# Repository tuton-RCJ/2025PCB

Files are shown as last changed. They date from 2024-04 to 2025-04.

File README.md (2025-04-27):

# 2025PCB
ツートンの基板・回路のリポジトリです。
ご自由にご覧下さい。

基板はすべてKiCAD7.0で設計し、JLCPCB様に発注しています。
1-TOKYOが東東京ノード大会で使用した基板です。
2-KANTOは関東ブロック大会で使用した基板です。
3-NAGOYAは名古屋全国大会で使用した基板です。

# 3-NAGOYA
全国大会機「シロ」の基板です。
全部で6枚です。
## 基板一覧
* 01 MAIN
    メイン基板。一層目に置きます。
* 02 LINE
    ラインセンサ基板。一層目に置きます。
    フォトリフレクタは16個使います。
* 03 FRONT
    正面基板。ToFセンサを搭載しています。
* 04 RESCUE
    二層目と一層目をつなぐ基板です。
* 05 PWR
    電源基板。メイン基板とスペーサで接続します。
* 06 UI
    UI基板。ディスプレイを搭載しています。使いませんでした。
* 07 OpenMV
    OpenMVに取り付けるシールドです。UARTをXHに引き出しました。

# 2-KANTO
関東機体「MIKE（ミケ）」の基板です。
今回は全部で3枚です。

## 基板一覧
* 01 MAIN
    メイン基板。一層目に置きます。
* 02 LINE
    ラインセンサ基板。一層目に置きます。
    フォトリフレクタは16個使います。
* 03 FRONT
    当初は作る予定だったが使わなくなりました。
    空っぽなのもつまらないので回路図に落書きしました。
* 04 PWR
    電源基板。二層目に置きます。

# 1-TOKYO
東東京機体「ポチ」の基板です。
全部で5枚（+α）です。

## 基板一覧
* 01 main
    メイン基板。
    * 完成 2024/10/01
    * 発注 2024/10/02
* 02 top
    ハンドルの上に置く基板。UI基板。
    * 設計中
    * 使わなかった
* 03 front
    正面の基板。カメラとToFを置く。
    * 完成 2024/10/01
    * 発注 2024/10/02
* 04 line
    ラインセンサ基板。
    * 完成 2024/06/25
    * 発注 2024/06/26
* 05 PWR
    電源基板。
    3.3V, 5V, 7.2Vを生成。
    * 完成 2024/06/25
    * 発注 2024/06/26
* 06 WRITER
    書き込み基板
    * 完成 2024/05/14
    * 発注 2024/05/16
* 07 frame
    フレームを基板で作ろうとしたが結局3Dプリンタで作った。
* 08 REG_mod
    TPS5430を使用した自作DCDC。
    電源基板に乗せる。
    * 完成 2024/06/25
    * 発注 2024/06/26
* 09 ToF_mod
    自作ToF（VL53L0X）
    * 完成　2024/08/17
## リポジトリ構成
* 01-main ~ 08-REG_mod 
    それぞれの基板のKiCADのプロジェクト。
* library
    KiCADで使用しているライブラリ。
    シンボル、フットプリント、3Dモデル。
* pin
    STM32のピン配置を考えるために使用したSTM32CubeIDEのファイル。
    かなり雑です。
* ver1、ver2
    過去作の保管場所。
    何らかの事情でボツになった設計たちです。
* PDFファイル
    完成した基板の回路図はPDFにしてあります。
    ブラウザ上で見ることができると思います。

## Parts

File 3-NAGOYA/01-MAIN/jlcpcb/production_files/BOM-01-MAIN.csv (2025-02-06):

Comment | Designator | Footprint | LCSC
FerriteBead | FB1 | R_0805_2012Metric | C1015
100n | C1,C10,C12,C13,C3,C4,C5,C6,C8,C9 | C_0402_1005Metric | C1525
10u | C14,C15 | C_0805_2012Metric | C15850
1k | R8 | R_0805_2012Metric | C17513
USB_C_Receptacle_USB2.0 | J4 | USB_C_Receptacle_GCT_USB4105-xx-A_16P_TopMnt_Horizontal | C19274016
LED_ORANGE | D4 | LED_0805_2012Metric | C2296
LED_GREEN | D1,D2,D3,D7,D8 | LED_0805_2012Metric | C2297
470 | R10,R12,R17,R18,R7 | R_0603_1608Metric | C23179
7.5k | R1 | R_0603_1608Metric | C23234
4.7u | C2,C7 | C_0402_1005Metric | C23733
10k | R13,R15,R2,R6 | R_0603_1608Metric | C25804
5.1k | R11,R9 | R_0805_2012Metric | C27834
20k | R3 | R_0603_1608Metric | C4184
2.2k | R14,R16,R4,R5 | R_0603_1608Metric | C4190
22u | L1,L2 | FXL1040-220-M | C475917
1u | C11 | C_0402_1005Metric | C52923
0.01u | C16,C17 | C_0603_1608Metric | C57112
MAX485ESA | U2 | SOP-8_3.9x4.9mm_P1.27mm | C668206
STM32F446RETx | U1 | LQFP-64_10x10mm_P0.5mm | C69336
SS34 | D5,D6 | D_SMA | C8678
TPS5430DDA | U7,U8 | TI_SO-PowerPAD-8_ThermalVias | C9864
CH340E | U6 | MSOP-10_3x3mm_P0.5mm | C99652
~ | U4 | BNO055
Front | J1 | JST_XH_B4B-XH-A_1x04_P2.50mm_Vertical
toLINE | J3 | JST_XH_B5B-XH-A_1x05_P2.50mm_Vertical
STS3032 | J5 | Molex_SPOX_5267-03A_1x03_P2.50mm_Vertical
2SA1015 | Q1 | TO-92_Inline
STS3032 | J8 | Molex_SPOX_5267-03A_1x03_P2.50mm_Vertical
STS3032 | J7 | Molex_SPOX_5267-03A_1x03_P2.50mm_Vertical
220u | C18 | CP_Radial_D6.3mm_P2.50mm
~ | U5 | vl53l0x_vertical
STS3032 | J6 | Molex_SPOX_5267-03A_1x03_P2.50mm_Vertical
~ | U3 | vl53l0x_vertical
Top | J2 | JST_XH_B4B-XH-A_1x04_P2.50mm_Vertical
220u | C19 | CP_Radial_D6.3mm_P2.50mm
Buzzer | BZ1 | Buzzer_15x7.5RM7.6
NRST | SW1 | THBP07-043Cx
BOOT0 | SW2 | THBP07-043Cx

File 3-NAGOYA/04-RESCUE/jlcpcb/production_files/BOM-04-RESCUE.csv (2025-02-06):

Comment | Designator | Footprint | LCSC
100n | C10,C11,C12,C14,C15,C8,C9 | C_0402_1005Metric | C1525
10k | R12,R13 | R_1206_3216Metric | C17902
1M | R10,R7,R8,R9 | R_0603_1608Metric | C22935
LED_GREEN | D1 | LED_0805_2012Metric | C2297
330 | R1,R2,R3,R6 | R_0603_1608Metric | C23138
470 | R11 | R_0603_1608Metric | C23179
4.7u | C13 | C_0402_1005Metric | C23733
10k | R4,R5 | R_0603_1608Metric | C25804
22u | C1,C2 | C_0805_2012Metric | C45783
LM358 | U1 | SOIC-8_3.9x4.9mm_P1.27mm | C5423
AMS1117-3.3 | U5 | SOT-223-3_TabPin2 | C6186
STM32F103RCTx | U4 | LQFP-64_10x10mm_P0.5mm | C8323
ServoArmRight | M4 | PinHeader_1x03_P2.54mm_Horizontal
MAIN | J2 | JST_XH_B4B-XH-A_1x04_P2.50mm_Vertical
OpenMV | J6 | JST_XH_B4B-XH-A_1x04_P2.50mm_Vertical
ServoHandLeft | M5 | PinHeader_1x03_P2.54mm_Horizontal
ServoArmLeft | M3 | PinHeader_1x03_P2.54mm_Horizontal
UI | J1 | JST_XH_S4B-XH-A_1x04_P2.50mm_Horizontal
ServoHandRight | M6 | PinHeader_1x03_P2.54mm_Horizontal
LOADCELL_L | J5 | JST_XH_S4B-XH-A_1x04_P2.50mm_Horizontal
~ | U2 | vl53l0x_vertical
LOADCELL_R | J3 | JST_XH_S4B-XH-A_1x04_P2.50mm_Horizontal
ServoBasketLeft | M1 | PinHeader_1x03_P2.54mm_Horizontal
~ | U3 | vl53l0x_vertical
WRITER CONN | J4 | PinSocket_2x04_P2.54mm_Vertical

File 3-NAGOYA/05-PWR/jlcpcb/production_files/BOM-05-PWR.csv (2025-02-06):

Comment | Designator | Footprint | LCSC
10uF | C3,C4 | C_0805_2012Metric | C15850
1k | R1 | R_0603_1608Metric | C21190
1.2k | R6,R7 | R_0603_1608Metric | C22765
1.5k | R4 | R_0603_1608Metric | C22843
10 | R3 | R_0603_1608Metric | C22859
330 | R2 | R_0603_1608Metric | C23138
680 | R5 | R_0603_1608Metric | C23228
10k | R8 | R_0603_1608Metric | C25804
22uF | C1,C2 | C_0805_2012Metric | C45783
Fuse | F1 | FUSE_3557-15
~ | U2 | OKL-T6-W12N-C-SMD
Q_PMOS_GDS | Q1 | TO-251-3_Vertical
SW_SPST | SW1 | AkizukiSmallRockerSwitchHorizontal
~ | U1 | OKL-T6-W12N-C-SMD

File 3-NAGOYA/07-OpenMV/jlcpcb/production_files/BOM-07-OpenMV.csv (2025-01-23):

Comment | Designator | Footprint | LCSC
Conn_01x04 | J3 | JST_XH_S4B-XH-A_1x04_P2.50mm_Horizontal
3V3IN | SW2 | SK-12D11VG3
5VIN | SW1 | SK-12D11VG3
REG | J4 | PinHeader_1x03_P2.54mm_Vertical
OpenMV2 | J2 | PinSocket_1x08_P2.54mm_Vertical
OpenMV1 | J1 | PinSocket_1x08_P2.54mm_Vertical
LED | D2 | LED_D3.0mm_Clear
5VLED | D1 | LED_D3.0mm_Clear

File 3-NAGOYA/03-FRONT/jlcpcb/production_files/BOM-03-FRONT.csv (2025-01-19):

Comment | Designator | Footprint | LCSC
MountingHole | H2 | MountingHole_3.2mm_M3
WS2812B | D1 | LED_WS2812B_PLCC4_5.0x5.0mm_P3.2mm
~ | U5 | VL53L0X_horizontal
WS2812B | D4 | LED_WS2812B_PLCC4_5.0x5.0mm_P3.2mm
WS2812B | D2 | LED_WS2812B_PLCC4_5.0x5.0mm_P3.2mm
~ | U2 | VL53L0X_horizontal
WS2812B | D5 | LED_WS2812B_PLCC4_5.0x5.0mm_P3.2mm
MountingHole | H1 | MountingHole_3.2mm_M3
~ | U4 | VL53L0X_horizontal
WS2812B | D3 | LED_WS2812B_PLCC4_5.0x5.0mm_P3.2mm
~ | U3 | VL53L0X_horizontal
~ | U1 | VL53L0X_horizontal
10k | R1 | R_Axial_DIN0207_L6.3mm_D2.5mm_P10.16mm_Horizontal
OpenMV Conn | J1 | JST_XH_B4B-XH-A_1x04_P2.50mm_Vertical
10k | R2 | R_Axial_DIN0207_L6.3mm_D2.5mm_P10.16mm_Horizontal
~ | U6 | MOUDLE14P-2.54-21X17.8MM

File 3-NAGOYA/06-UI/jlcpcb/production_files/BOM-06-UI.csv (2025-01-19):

Comment | Designator | Footprint | LCSC
OpenMV Conn | J1 | JST_XH_S4B-XH-A_1x04_P2.50mm_Horizontal
~ | U1 | MOUDLE14P-SMD-2.54-21X17.8MM
~ | U2 | MS2807
SW_Push | SW1 | SW_PUSH-12mm
R | R1 | R_Axial_DIN0207_L6.3mm_D2.5mm_P10.16mm_Horizontal
MountingHole | H2 | MountingHole_3.2mm_M3
MountingHole | H1 | MountingHole_3.2mm_M3
WS2812B | D8 | LED_WS2812B_PLCC4_5.0x5.0mm_P3.2mm
WS2812B | D7 | LED_WS2812B_PLCC4_5.0x5.0mm_P3.2mm
WS2812B | D6 | LED_WS2812B_PLCC4_5.0x5.0mm_P3.2mm
WS2812B | D5 | LED_WS2812B_PLCC4_5.0x5.0mm_P3.2mm
WS2812B | D4 | LED_WS2812B_PLCC4_5.0x5.0mm_P3.2mm
WS2812B | D3 | LED_WS2812B_PLCC4_5.0x5.0mm_P3.2mm
WS2812B | D2 | LED_WS2812B_PLCC4_5.0x5.0mm_P3.2mm
WS2812B | D1 | LED_WS2812B_PLCC4_5.0x5.0mm_P3.2mm

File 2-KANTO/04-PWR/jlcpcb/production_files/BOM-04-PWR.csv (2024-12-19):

Comment | Designator | Footprint | LCSC
100n | C1,C2,C3,C4,C5,C6 | C_0402_1005Metric | C1525
10uF | C10,C11 | C_0805_2012Metric | C15850
1k | R7 | R_0603_1608Metric | C21190
1.2k | R12,R13 | R_0603_1608Metric | C22765
1.5k | R10 | R_0603_1608Metric | C22843
10 | R9 | R_0603_1608Metric | C22859
LED_GREEN | D1 | LED_0805_2012Metric | C2297
330 | R8 | R_0603_1608Metric | C23138
470 | R5 | R_0603_1608Metric | C23179
680 | R11 | R_0603_1608Metric | C23228
4.7u | C7 | R_0402_1005Metric | C23733
10k | R1,R2,R3,R4,R6 | R_0603_1608Metric | C25804
22uF | C8,C9 | C_0805_2012Metric | C45783
STM32F103C8Tx | U1 | LQFP-48_7x7mm_P0.5mm | C8734
~ | U5 | OKL-T6-W12N-C-SMD
SW_SPST | SW2 | AkizukiSmallRockerSwitchHorizontal
~ | U4 | OKL-T6-W12N-C-SMD
MAIN Conn | J5 | JST_XH_S8B-XH-A_1x08_P2.50mm_Horizontal
ServoHandRight | M6 | PinHeader_1x03_P2.54mm_Horizontal
Fuse | F1 | FUSE_3557-15
~ | U2 | vl53l0x_vertical
WRITER CONN | J4 | PinSocket_2x04_P2.54mm_Horizontal
~ | U3 | vl53l0x_vertical
Conn_01x05 | J2 | PinHeader_1x05_P2.54mm_Vertical
ServoArmRight | M4 | PinHeader_1x03_P2.54mm_Horizontal
ServoHandLeft | M5 | PinHeader_1x03_P2.54mm_Horizontal
voltmeter | J7 | JST_XH_S2B-XH-A_1x02_P2.50mm_Horizontal
OpenMV Conn | J6 | JST_XH_S4B-XH-A_1x04_P2.50mm_Horizontal
Q_PMOS_GDS | Q1 | TO-251-3_Vertical
PA_PIN | J3 | PinHeader_1x16_P2.54mm_Vertical
ServoArmLeft | M3 | PinHeader_1x03_P2.54mm_Horizontal
PB_PIN | J1 | PinHeader_1x16_P2.54mm_Vertical
SW_SPDT | SW1 | SK-12D11VG3
ServoBasketLeft | M1 | PinHeader_1x03_P2.54mm_Vertical

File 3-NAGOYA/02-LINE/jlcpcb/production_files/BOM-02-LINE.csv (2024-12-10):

Comment | Designator | Footprint | LCSC
FerriteBead | FB1 | R_0805_2012Metric | C1015
100n | C1,C3,C4,C5,C6,C8,C9 | C_0402_1005Metric | C1525
1k | R16,R17,R18,R19,R20,R21,R22,R23,R32,R33,R34,R35,R36,R37,R38,R39 | R_0603_1608Metric | C21190
120 | R10,R11,R12,R13,R14,R15,R24,R25,R26,R27,R28,R29,R30,R31,R8,R9 | R_0603_1608Metric | C22787
LED_GREEN | D1 | LED_0805_2012Metric | C2297
470 | R3 | R_0603_1608Metric | C23179
4.7u | C2,C7 | C_0402_1005Metric | C23733
10k | R1,R2 | R_0603_1608Metric | C25804
1u | C10 | C_0402_1005Metric | C52923
STM32F446RETx | U1 | LQFP-64_10x10mm_P0.5mm | C69336
Conn_01x05 | J3 | JST_XH_B5B-XH-A_1x05_P2.50mm_Vertical
~ | U16 | LBR127HLD
WS2812B | D5 | LED_WS2812B_PLCC4_5.0x5.0mm_P3.2mm
WS2812B | D6 | LED_WS2812B_PLCC4_5.0x5.0mm_P3.2mm
WS2812B | D4 | LED_WS2812B_PLCC4_5.0x5.0mm_P3.2mm
~ | U17 | LBR127HLD
~ | U7 | LBR127HLD
~ | U6 | LBR127HLD
~ | U3 | LBR127HLD
~ | U9 | LBR127HLD
~ | U12 | LBR127HLD
~ | U8 | LBR127HLD
~ | U10 | LBR127HLD
~ | U5 | LBR127HLD
~ | U14 | LBR127HLD
WS2812B | D3 | LED_WS2812B_PLCC4_5.0x5.0mm_P3.2mm
~ | U2 | LBR127HLD
~ | U13 | LBR127HLD
WS2812B | D2 | LED_WS2812B_PLCC4_5.0x5.0mm_P3.2mm
WS2812B | D7 | LED_WS2812B_PLCC4_5.0x5.0mm_P3.2mm
~ | U11 | LBR127HLD
~ | U4 | LBR127HLD
WRITER CONN | J2 | PinSocket_2x04_P2.54mm_Vertical
~ | U15 | LBR127HLD
~ | U19 | S9706
~ | U18 | S9706

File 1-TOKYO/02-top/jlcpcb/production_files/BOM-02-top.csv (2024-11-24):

Comment | Designator | Footprint | LCSC
ToTop | J1 | JST_XH_B4B-XH-A_1x04_P2.50mm_Vertical
SW_Push | SW3 | SW_PUSH_6mm
SW_Push | SW2 | SW_PUSH_6mm
SW_Push | SW1 | SW_PUSH_6mm
WS2812B | D3 | LED_WS2812B_PLCC4_5.0x5.0mm_P3.2mm
WS2812B | D4 | LED_WS2812B_PLCC4_5.0x5.0mm_P3.2mm
WS2812B | D6 | LED_WS2812B_PLCC4_5.0x5.0mm_P3.2mm
SSD1306 | J2 | PinHeader_1x04_P2.54mm_Vertical
WS2812B | D2 | LED_WS2812B_PLCC4_5.0x5.0mm_P3.2mm
SW_SPDT | SW4 | PinHeader_1x03_P2.54mm_Vertical
WS2812B | D1 | LED_WS2812B_PLCC4_5.0x5.0mm_P3.2mm
WS2812B | D5 | LED_WS2812B_PLCC4_5.0x5.0mm_P3.2mm
~ | U1 | XIAO_Board
10k | R1 | R_Axial_DIN0207_L6.3mm_D2.5mm_P10.16mm_Horizontal
10k | R3 | R_Axial_DIN0207_L6.3mm_D2.5mm_P10.16mm_Horizontal
10k | R2 | R_Axial_DIN0207_L6.3mm_D2.5mm_P10.16mm_Horizontal
10k | R4 | R_Axial_DIN0207_L6.3mm_D2.5mm_P10.16mm_Horizontal

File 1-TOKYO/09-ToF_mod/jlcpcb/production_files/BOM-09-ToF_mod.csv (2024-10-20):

Comment | Designator | Footprint | LCSC
0.1u | C1 | C_0603_1608Metric | C14663
4.7u | C2 | C_0603_1608Metric | C19666
1.5k | R2,R3 | R_0603_1608Metric | C22843
10k | R1,R4 | R_0603_1608Metric | C25804
VL53L0X | U1 | ST_VL53L0X | C91199
Conn_01x02 | J2 | PinHeader_1x02_P2.54mm_Vertical
Conn_01x04 | J1 | PinHeader_1x04_P2.54mm_Vertical

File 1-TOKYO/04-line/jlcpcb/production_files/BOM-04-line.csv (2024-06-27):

Comment | Designator | Footprint | LCSC
100n | C3,C6 | C_0402_1005Metric | C1525
1k | R10,R11,R12,R13,R14,R15,R16,R17,R18,R28,R29,R30,R31,R32,R33,R34 | R_0603_1608Metric | C21190
120 | R1,R19,R2,R20,R21,R22,R23,R24,R25,R3,R4,R5,R6,R7,R8,R9 | R_0603_1608Metric | C22787
WS2812B | D1,D2,D4,D5,D6,D8 | LED_WS2812B_PLCC4_5.0x5.0mm_P3.2mm | C2843785
Conn_01x18 | J1 | PinHeader_1x18_P2.54mm_Vertical
CS_L | J3 | PinHeader_2x03_P2.54mm_Vertical
~ | U2 | LBR127HLD
~ | U15 | LBR127HLD
~ | U14 | LBR127HLD
~ | U25 | S11059
~ | U7 | LBR127HLD
~ | U4 | LBR127HLD
~ | U5 | LBR127HLD
~ | U16 | LBR127HLD
~ | U17 | LBR127HLD
~ | U8 | LBR127HLD
~ | U12 | LBR127HLD
~ | U3 | LBR127HLD
~ | U26 | S11059
~ | U9 | LBR127HLD
~ | U18 | LBR127HLD
~ | U6 | LBR127HLD
~ | U10 | LBR127HLD
~ | U13 | LBR127HLD
CS_R | J2 | PinHeader_2x03_P2.54mm_Vertical

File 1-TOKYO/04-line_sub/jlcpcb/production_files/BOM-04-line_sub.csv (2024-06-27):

Comment | Designator | Footprint | LCSC
FerriteBead | FB1 | R_0805_2012Metric | C1015
100n | C1,C3,C4,C5,C6,C8,C9 | C_0402_1005Metric | C1525
1u | C10 | C_0603_1608Metric | C15849
10k | R1,R2,R4,R5,R6,R7 | R_0805_2012Metric | C17414
LED_GREEN | D1 | LED_0805_2012Metric | C2297
470 | R3 | R_0603_1608Metric | C23179
4.7u | C2,C7 | C_0402_1005Metric | C23733
STM32F446RETx | U1 | LQFP-64_10x10mm_P0.5mm | C69336
Conn_01x18 | J4 | PinHeader_1x18_P2.54mm_Vertical
CS_R | J3 | PinHeader_2x03_P2.54mm_Vertical
Conn_01x06 | J1 | JST_XH_B6B-XH-A_1x06_P2.50mm_Vertical
WRITER CONN | J2 | PinHeader_2x04_P2.54mm_Vertical
CS_L | J5 | PinHeader_2x03_P2.54mm_Vertical

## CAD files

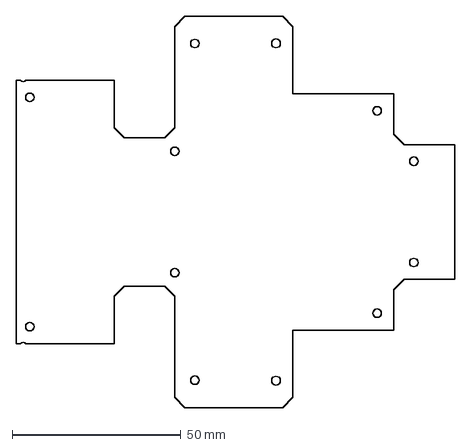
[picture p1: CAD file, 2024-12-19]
2-KANTO/01-MAIN/01-main-outline.dxf
130.0 x 116.0 mm

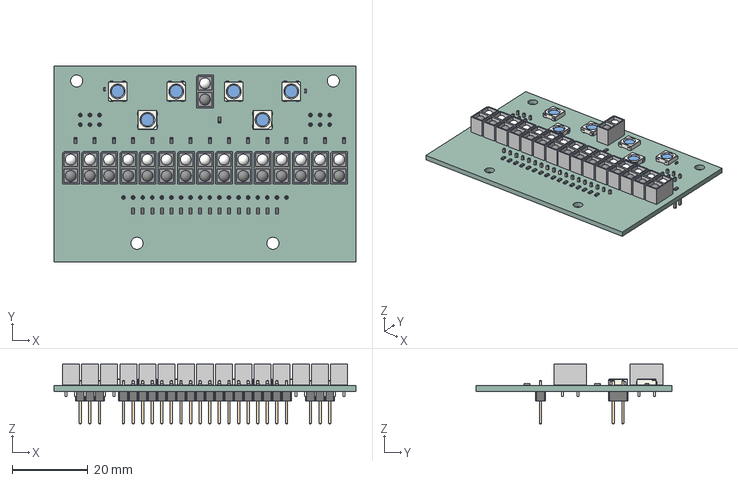
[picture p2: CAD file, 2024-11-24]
1-TOKYO/04-line/04-line.step
80.0 x 52.0 x 15.8 mm
04-line PCB

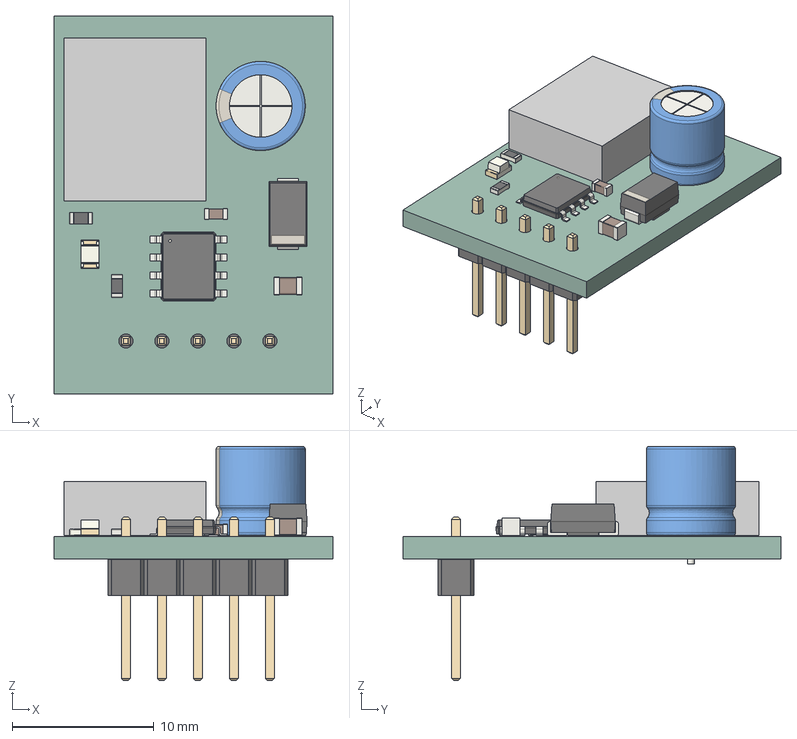
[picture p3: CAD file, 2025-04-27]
1-TOKYO/08-REG_mod/08-REG_mod_horizontal.step
19.7 x 26.7 x 16.5 mm
_autosave-08-REG_mod PCB

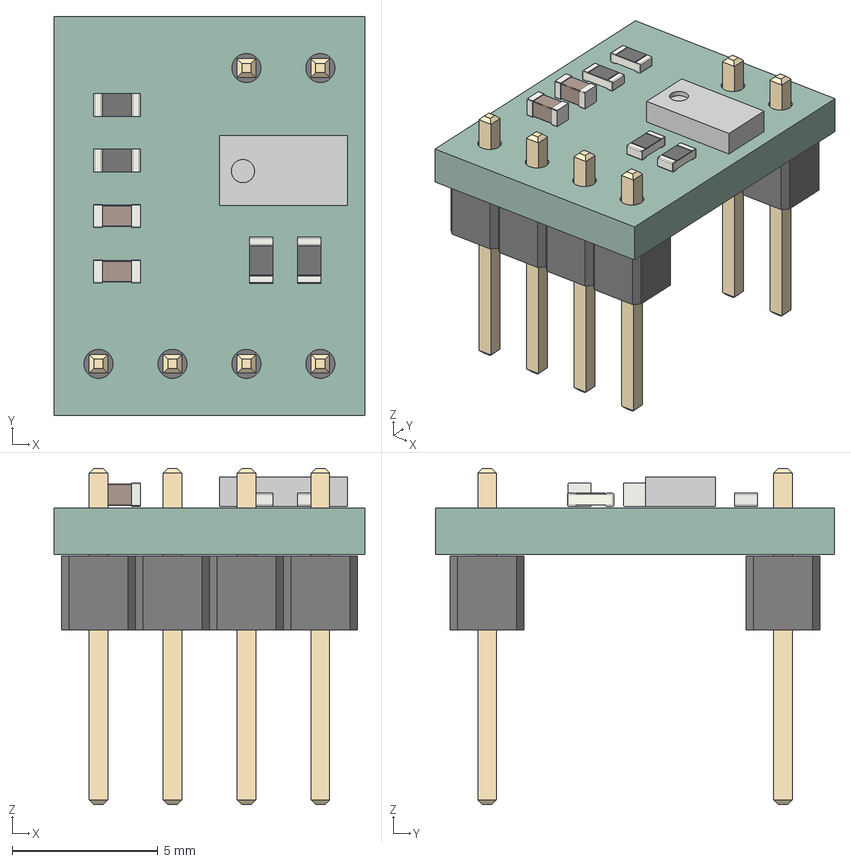
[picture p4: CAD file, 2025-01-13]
1-TOKYO/09-ToF_mod/09-ToF_mod_horizontal.step
10.7 x 13.7 x 11.5 mm
09-ToF_mod PCB

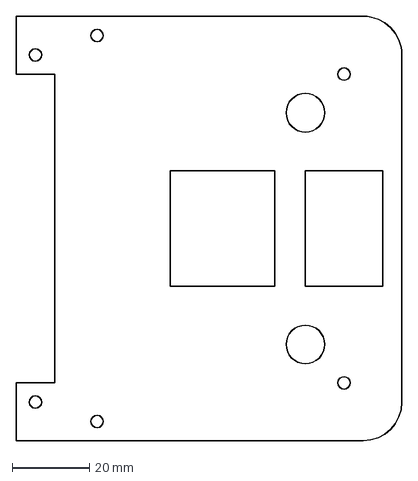
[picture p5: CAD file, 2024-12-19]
2-KANTO/04-PWR/POWER_OUTLINE.dxf
100.0 x 110.0 mm

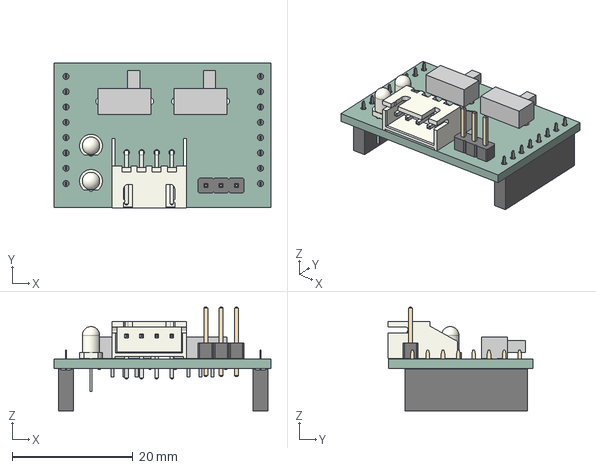
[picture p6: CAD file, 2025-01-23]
3-NAGOYA/07-OpenMV/07-OpenMV.step
36.0 x 24.0 x 17.2 mm
_autosave-07-OpenMV PCB

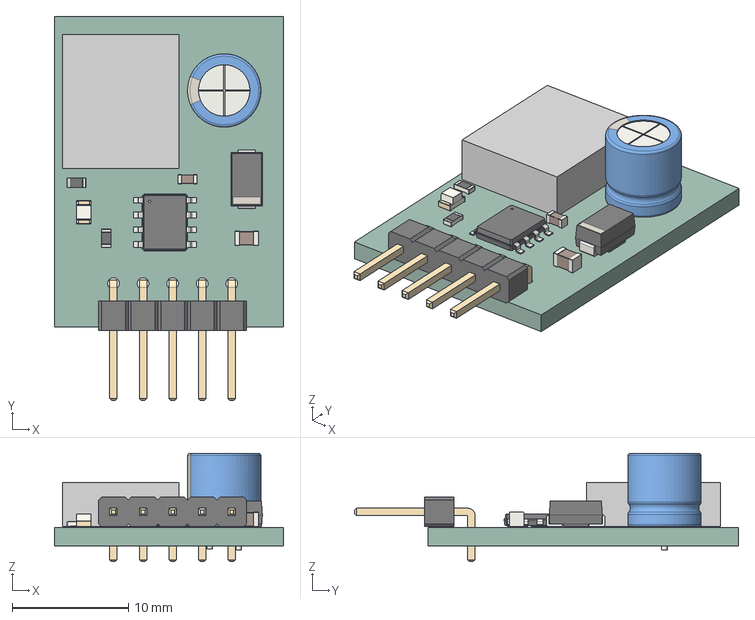
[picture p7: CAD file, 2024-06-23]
1-TOKYO/08-REG_mod/08-REG_mod.step
19.7 x 33.0 x 9.30 mm
08-REG_mod PCB

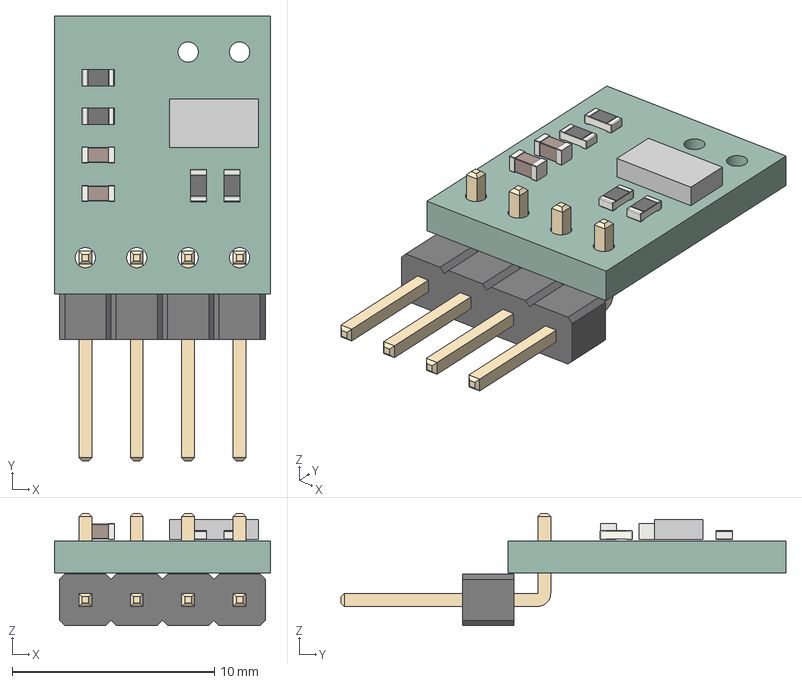
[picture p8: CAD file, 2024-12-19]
1-TOKYO/09-ToF_mod/09-ToF_mod_vertical.step
10.7 x 22.0 x 5.54 mm
09-ToF_mod PCB

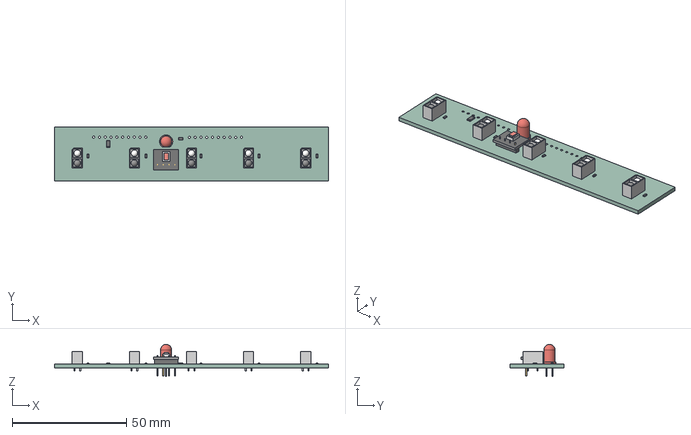
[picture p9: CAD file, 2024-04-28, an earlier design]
1-TOKYO/ver1/03-front/03-front.step
120.0 x 23.6 x 14.1 mm
03-front PCB

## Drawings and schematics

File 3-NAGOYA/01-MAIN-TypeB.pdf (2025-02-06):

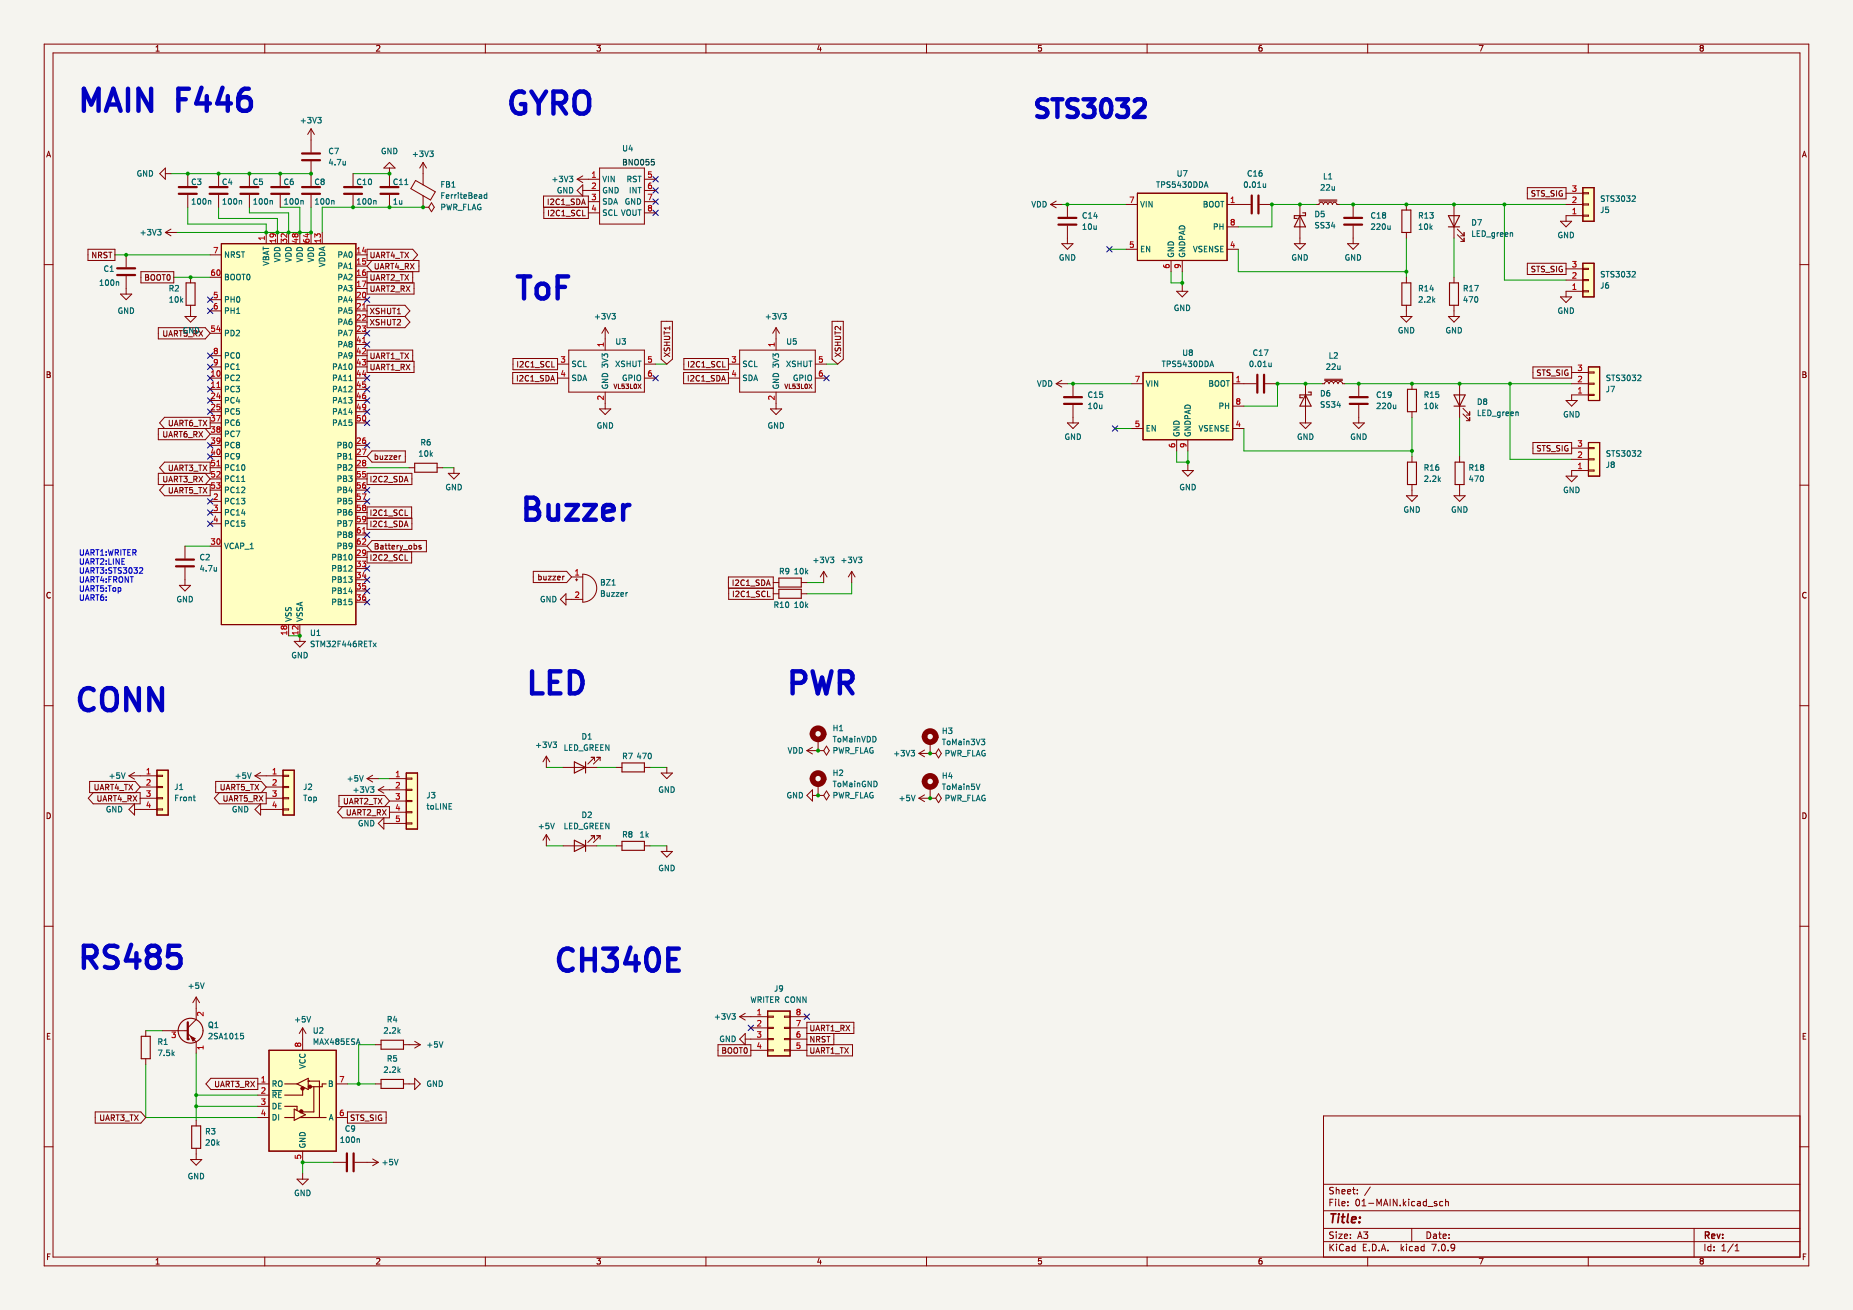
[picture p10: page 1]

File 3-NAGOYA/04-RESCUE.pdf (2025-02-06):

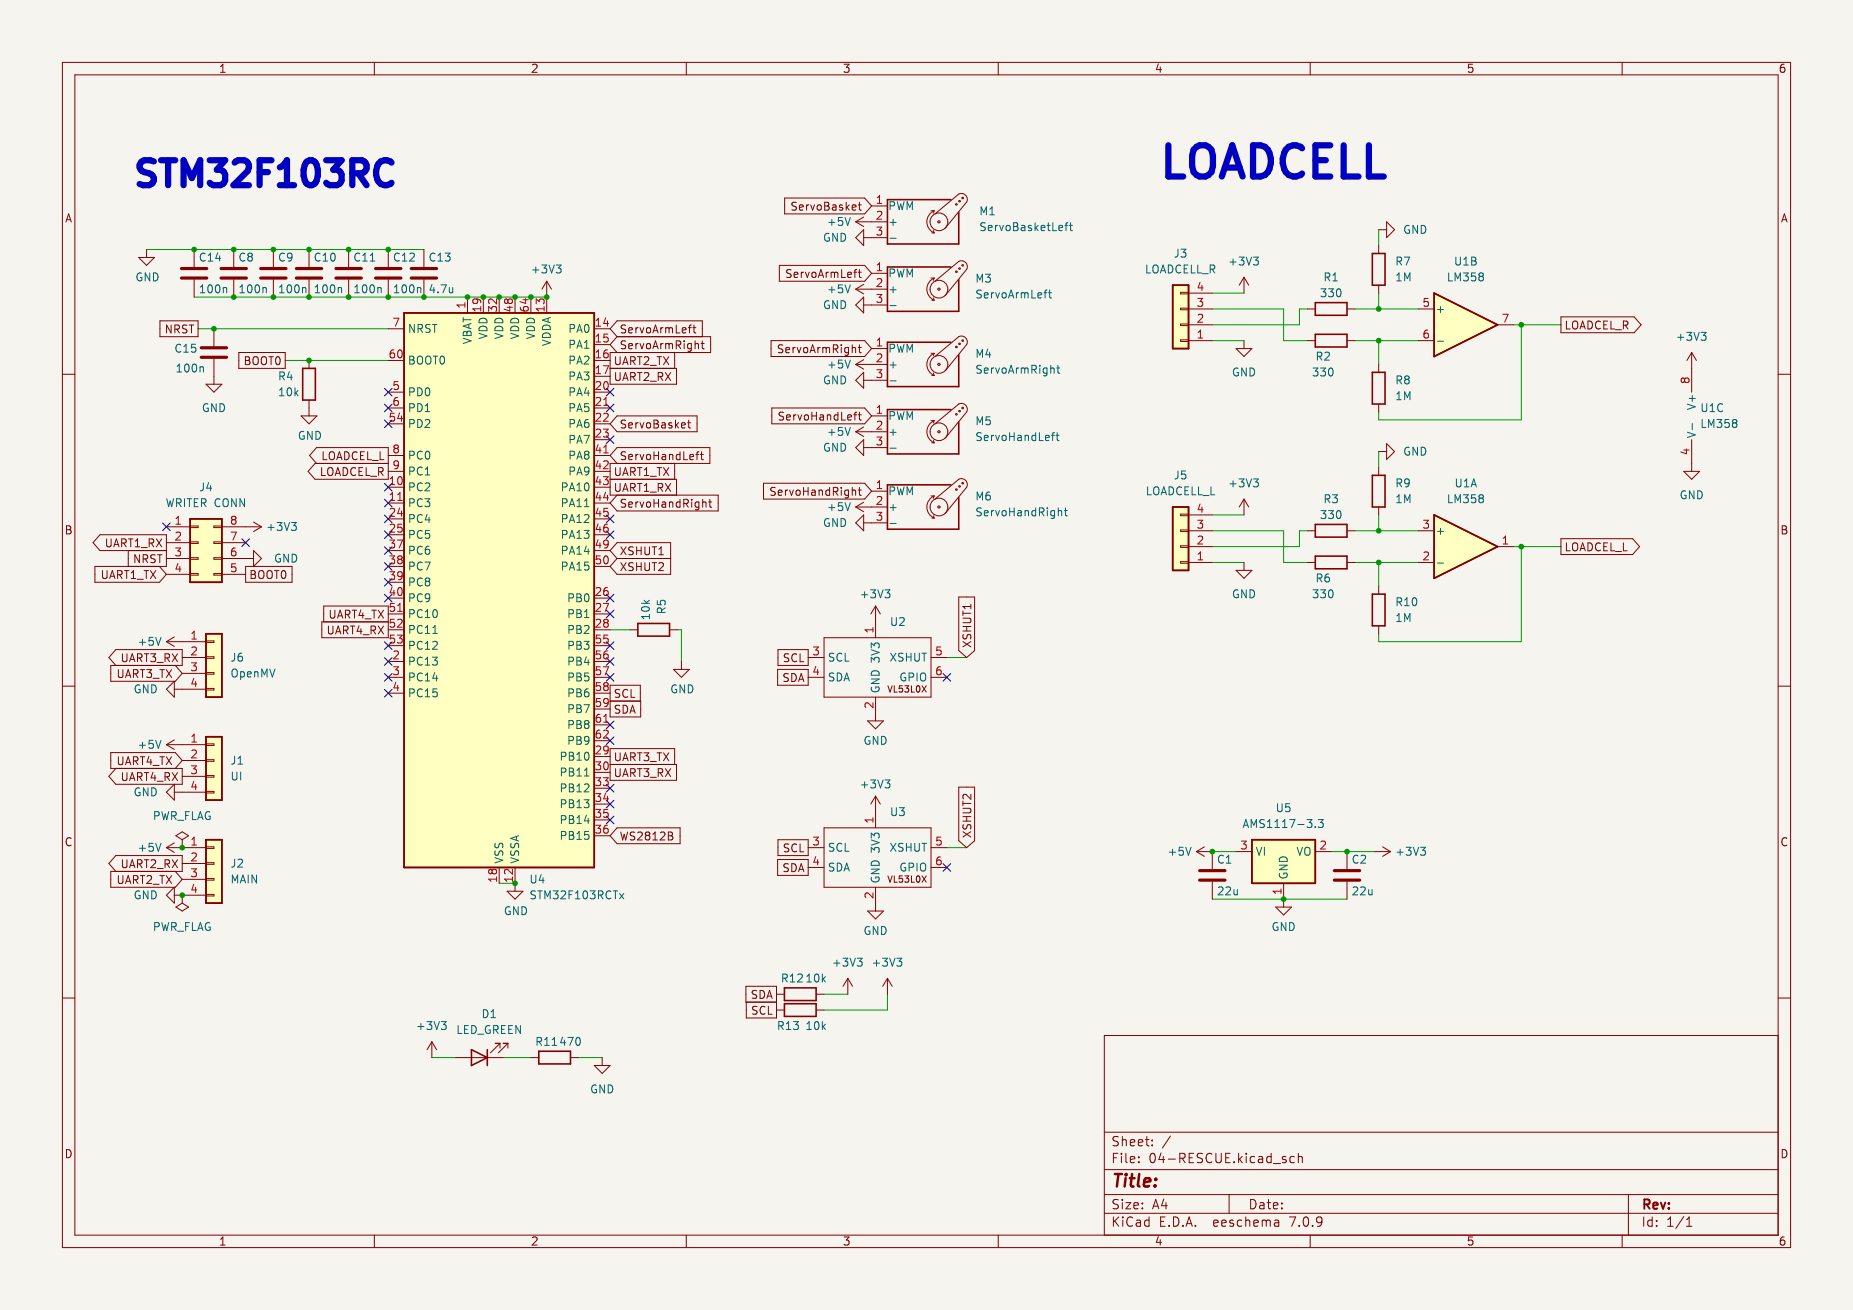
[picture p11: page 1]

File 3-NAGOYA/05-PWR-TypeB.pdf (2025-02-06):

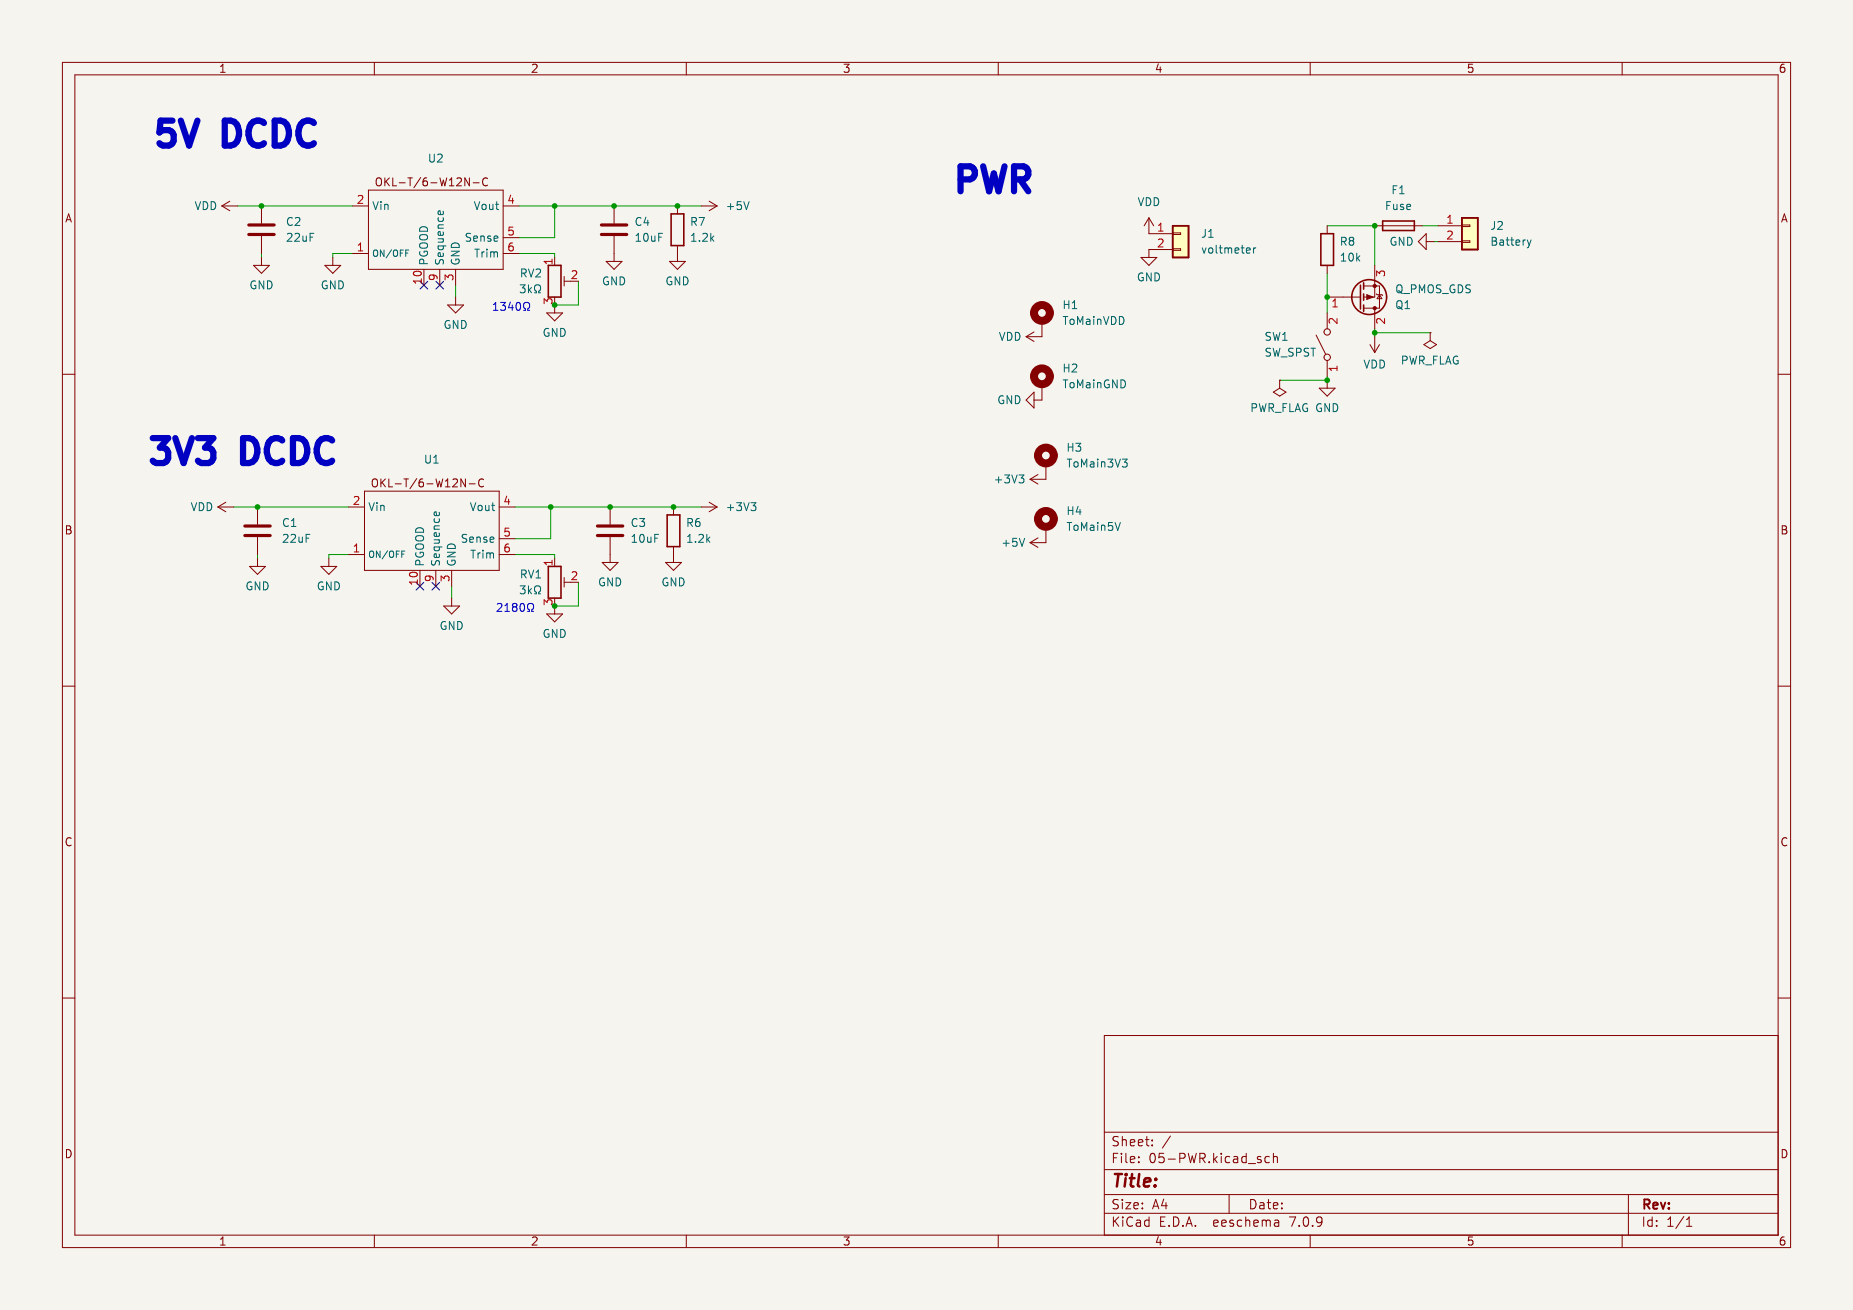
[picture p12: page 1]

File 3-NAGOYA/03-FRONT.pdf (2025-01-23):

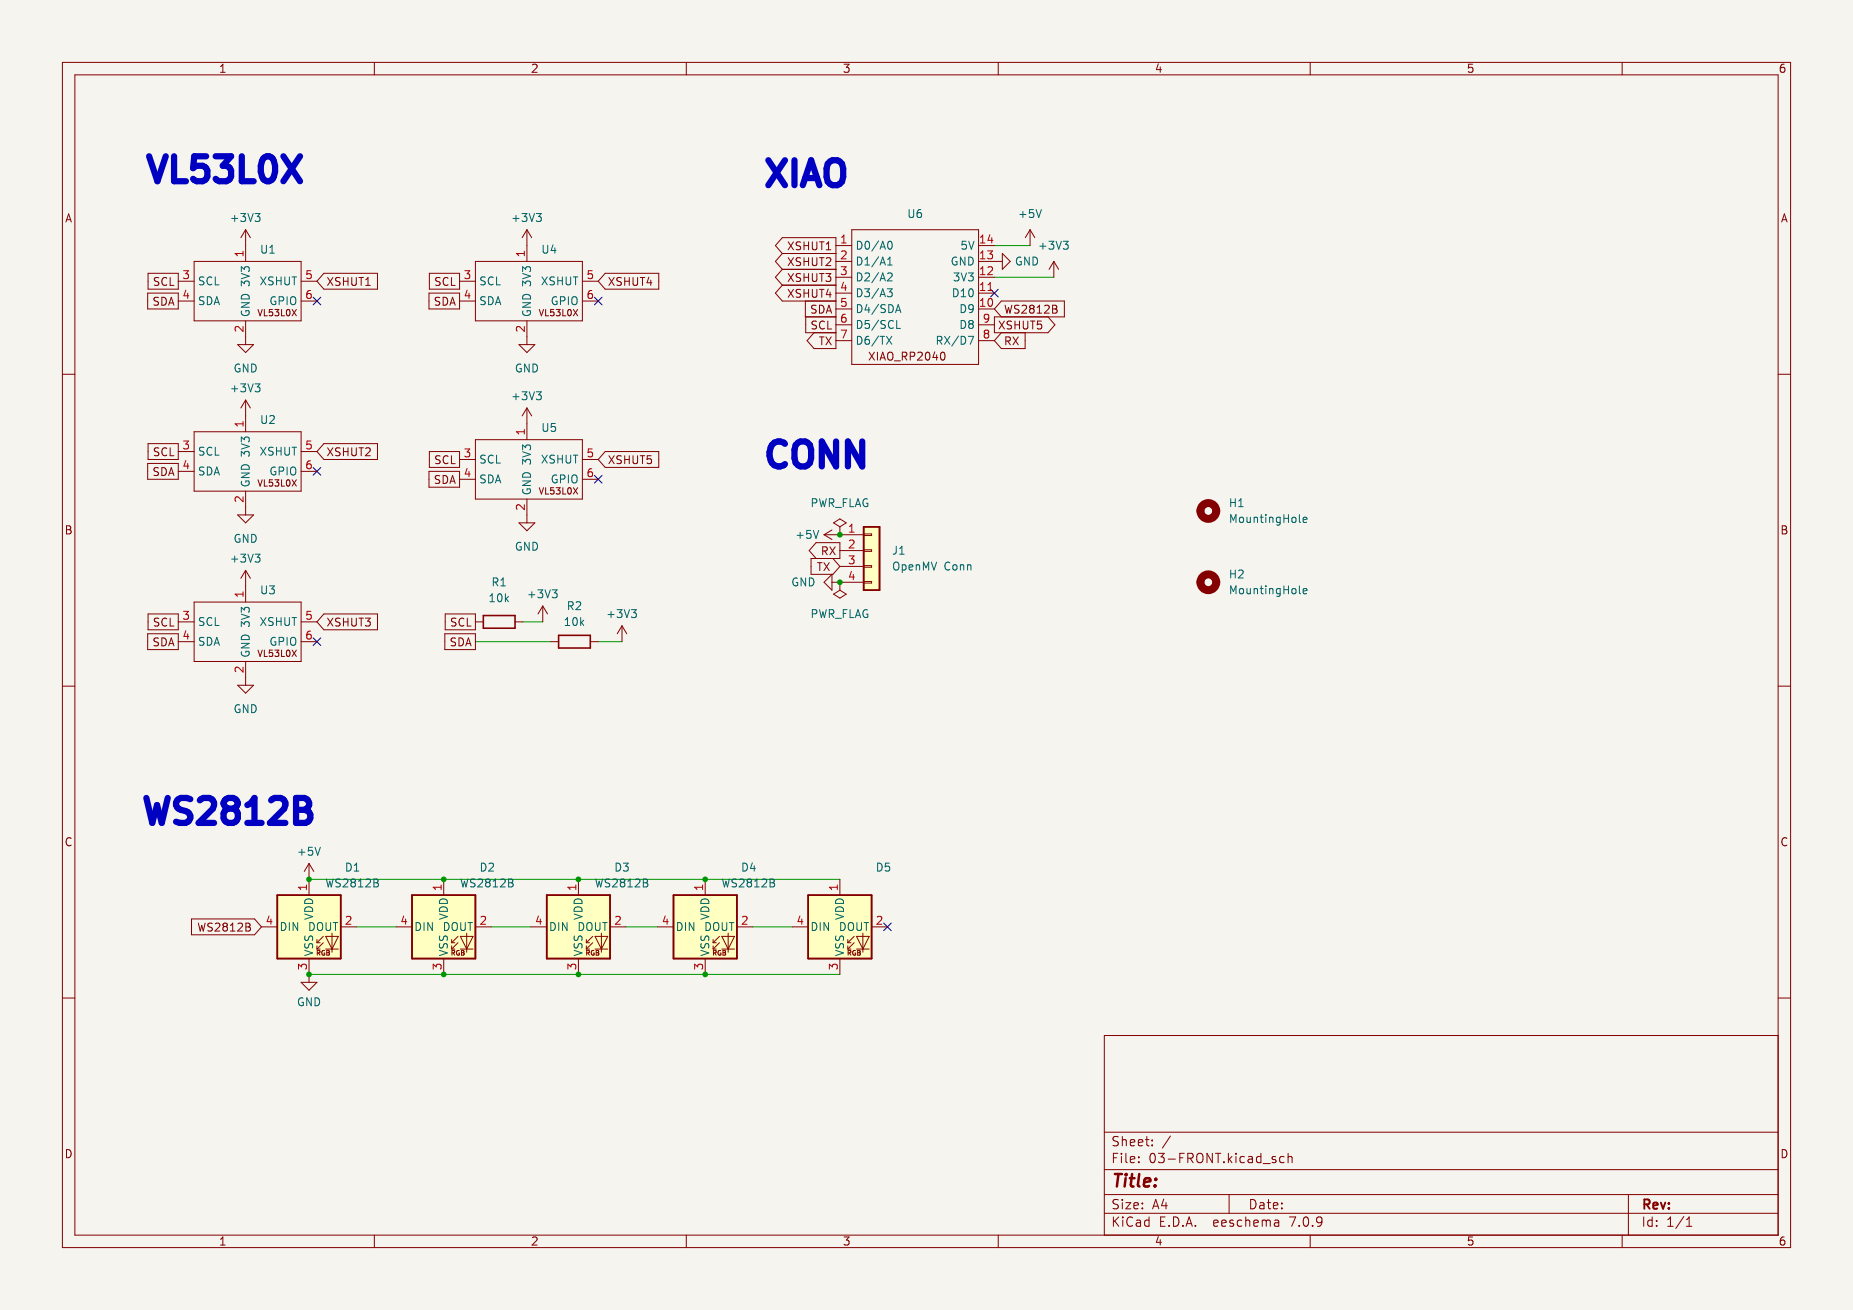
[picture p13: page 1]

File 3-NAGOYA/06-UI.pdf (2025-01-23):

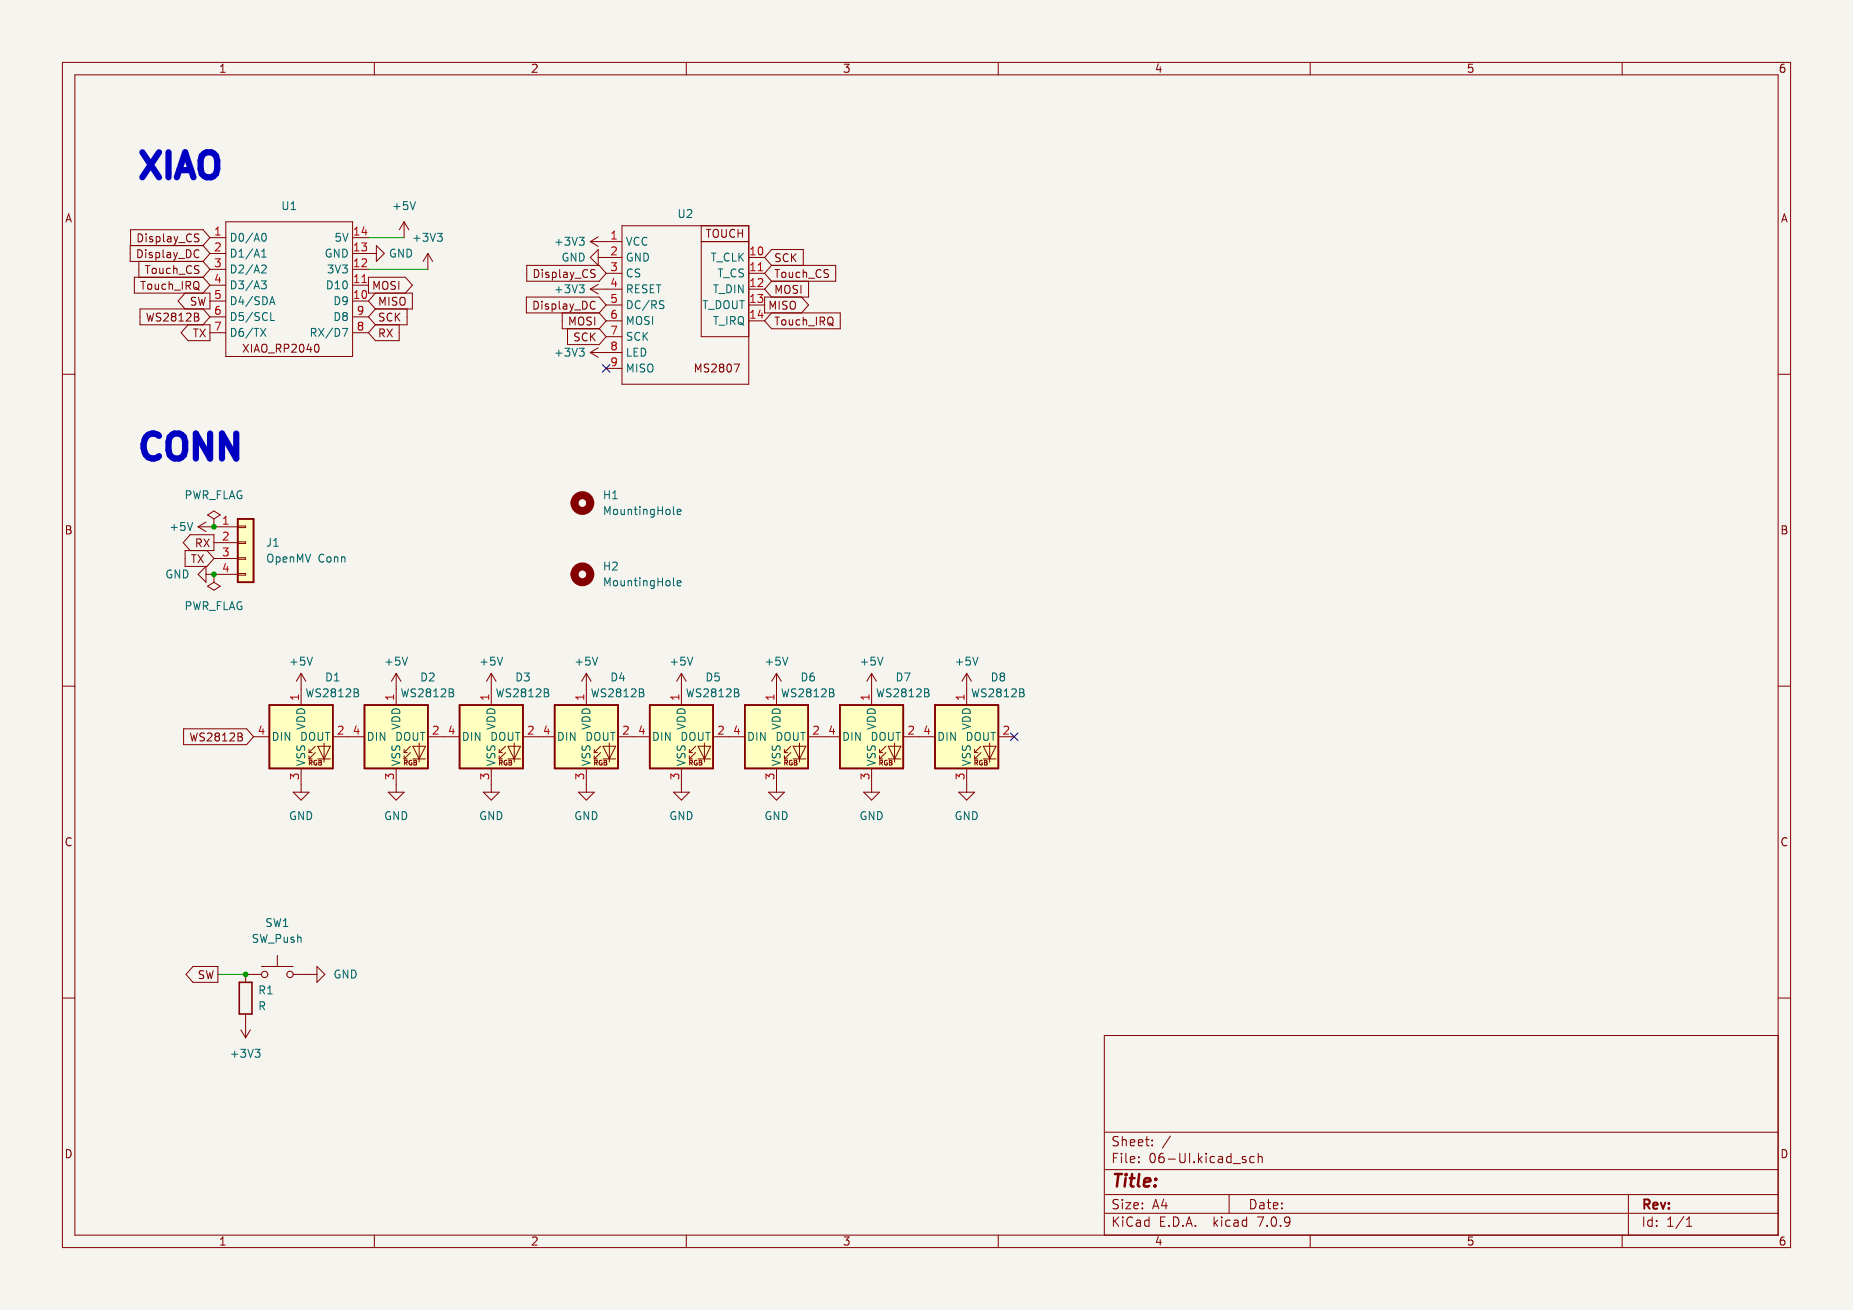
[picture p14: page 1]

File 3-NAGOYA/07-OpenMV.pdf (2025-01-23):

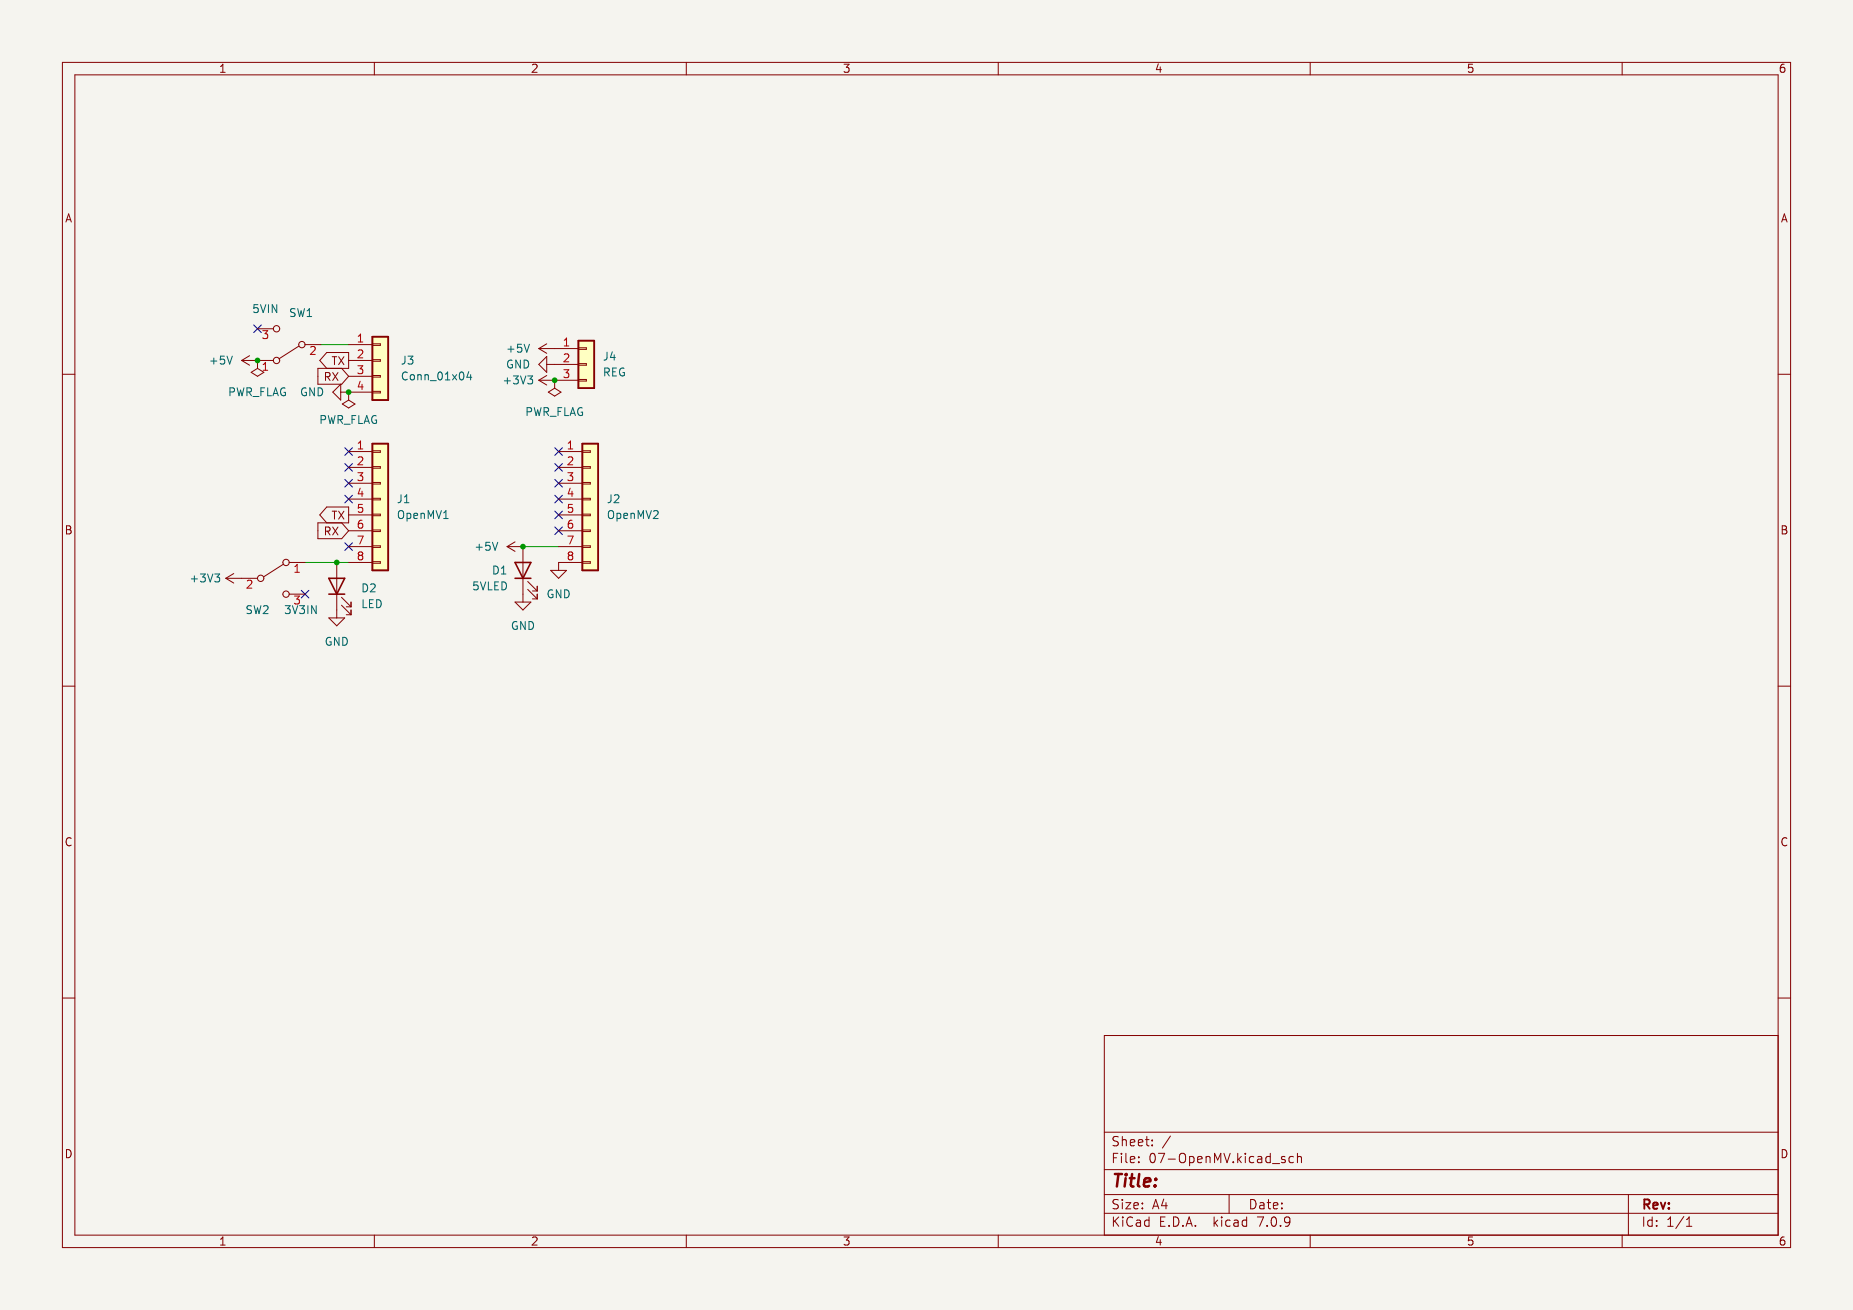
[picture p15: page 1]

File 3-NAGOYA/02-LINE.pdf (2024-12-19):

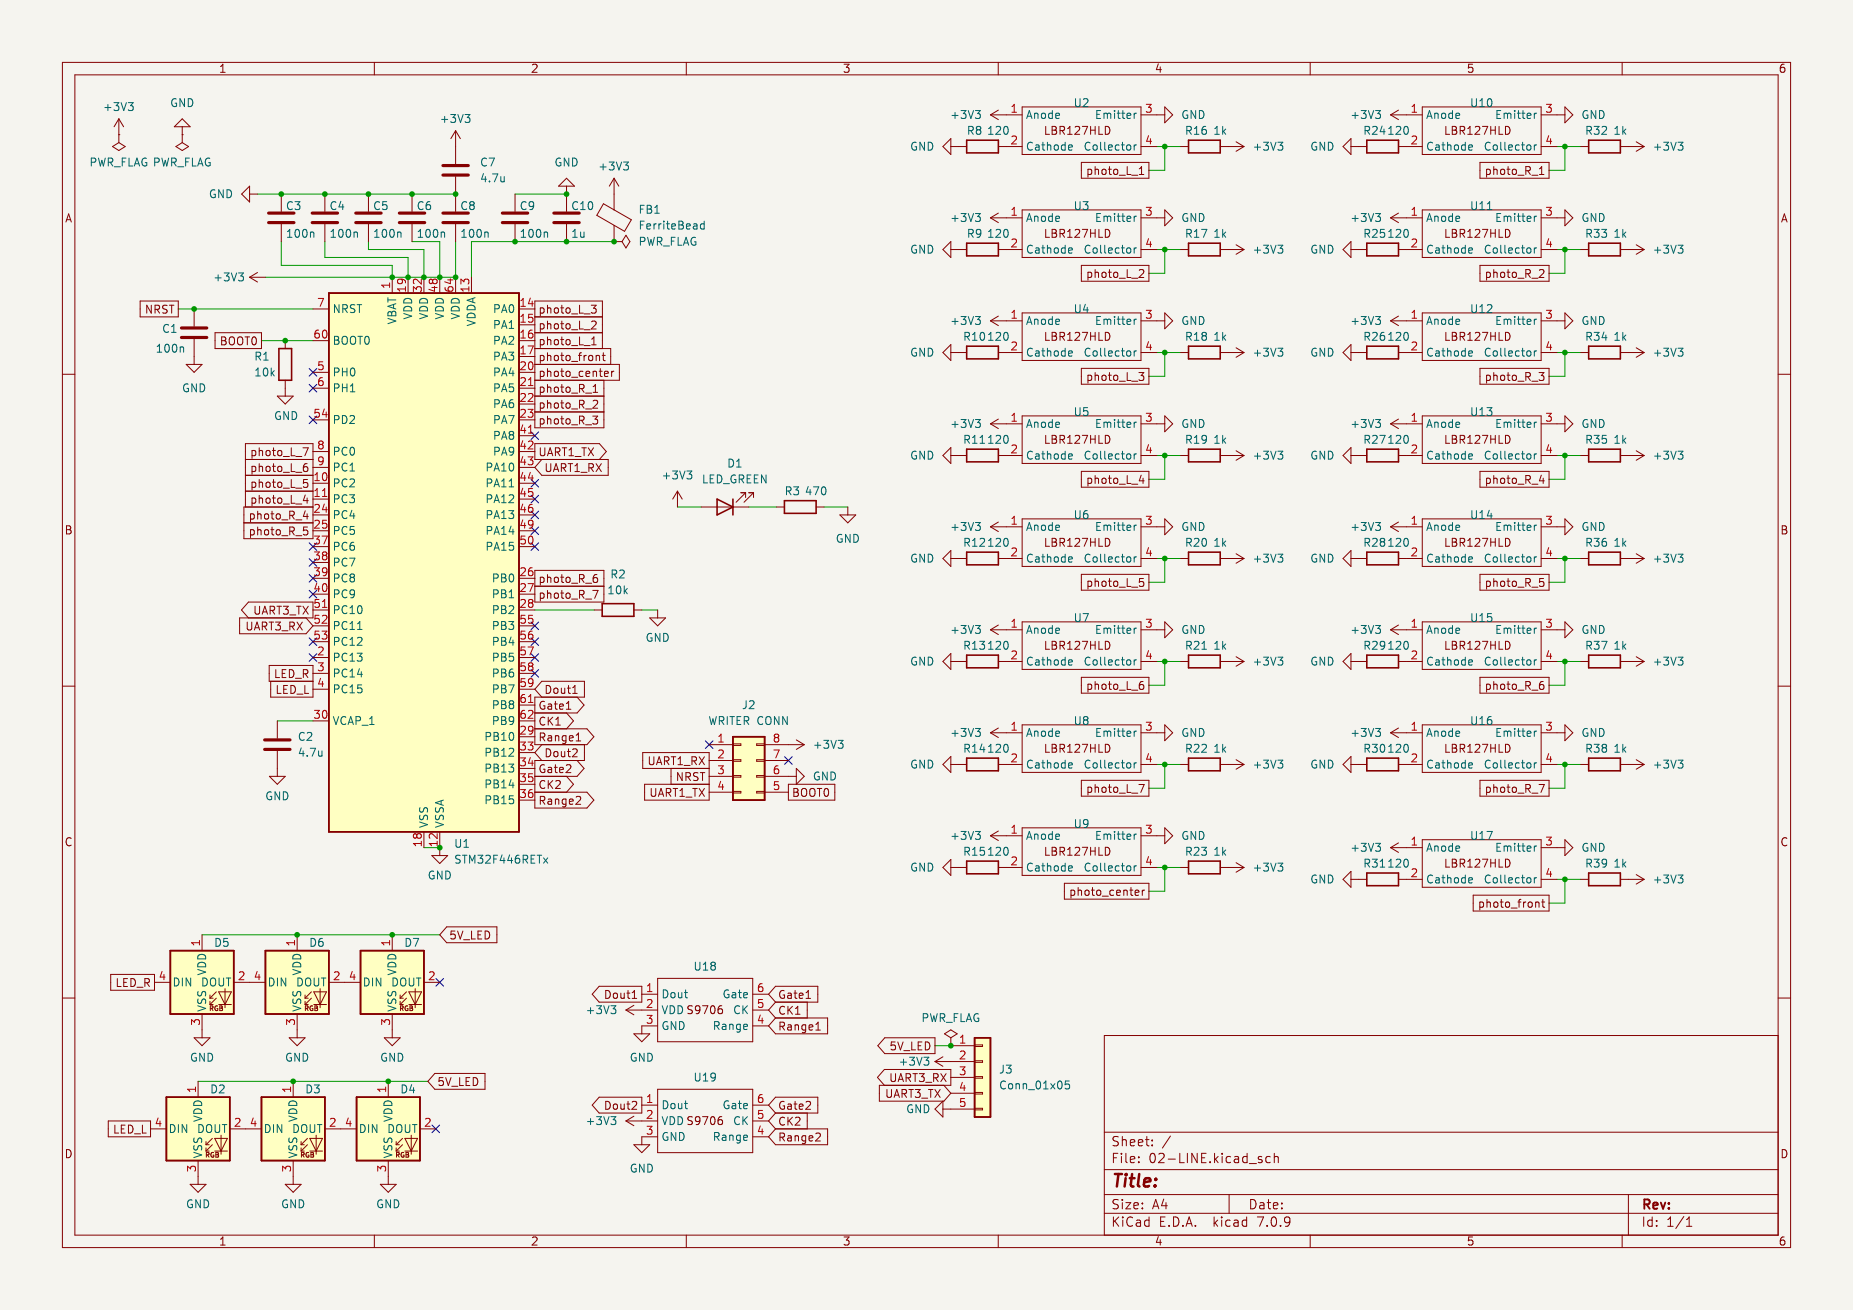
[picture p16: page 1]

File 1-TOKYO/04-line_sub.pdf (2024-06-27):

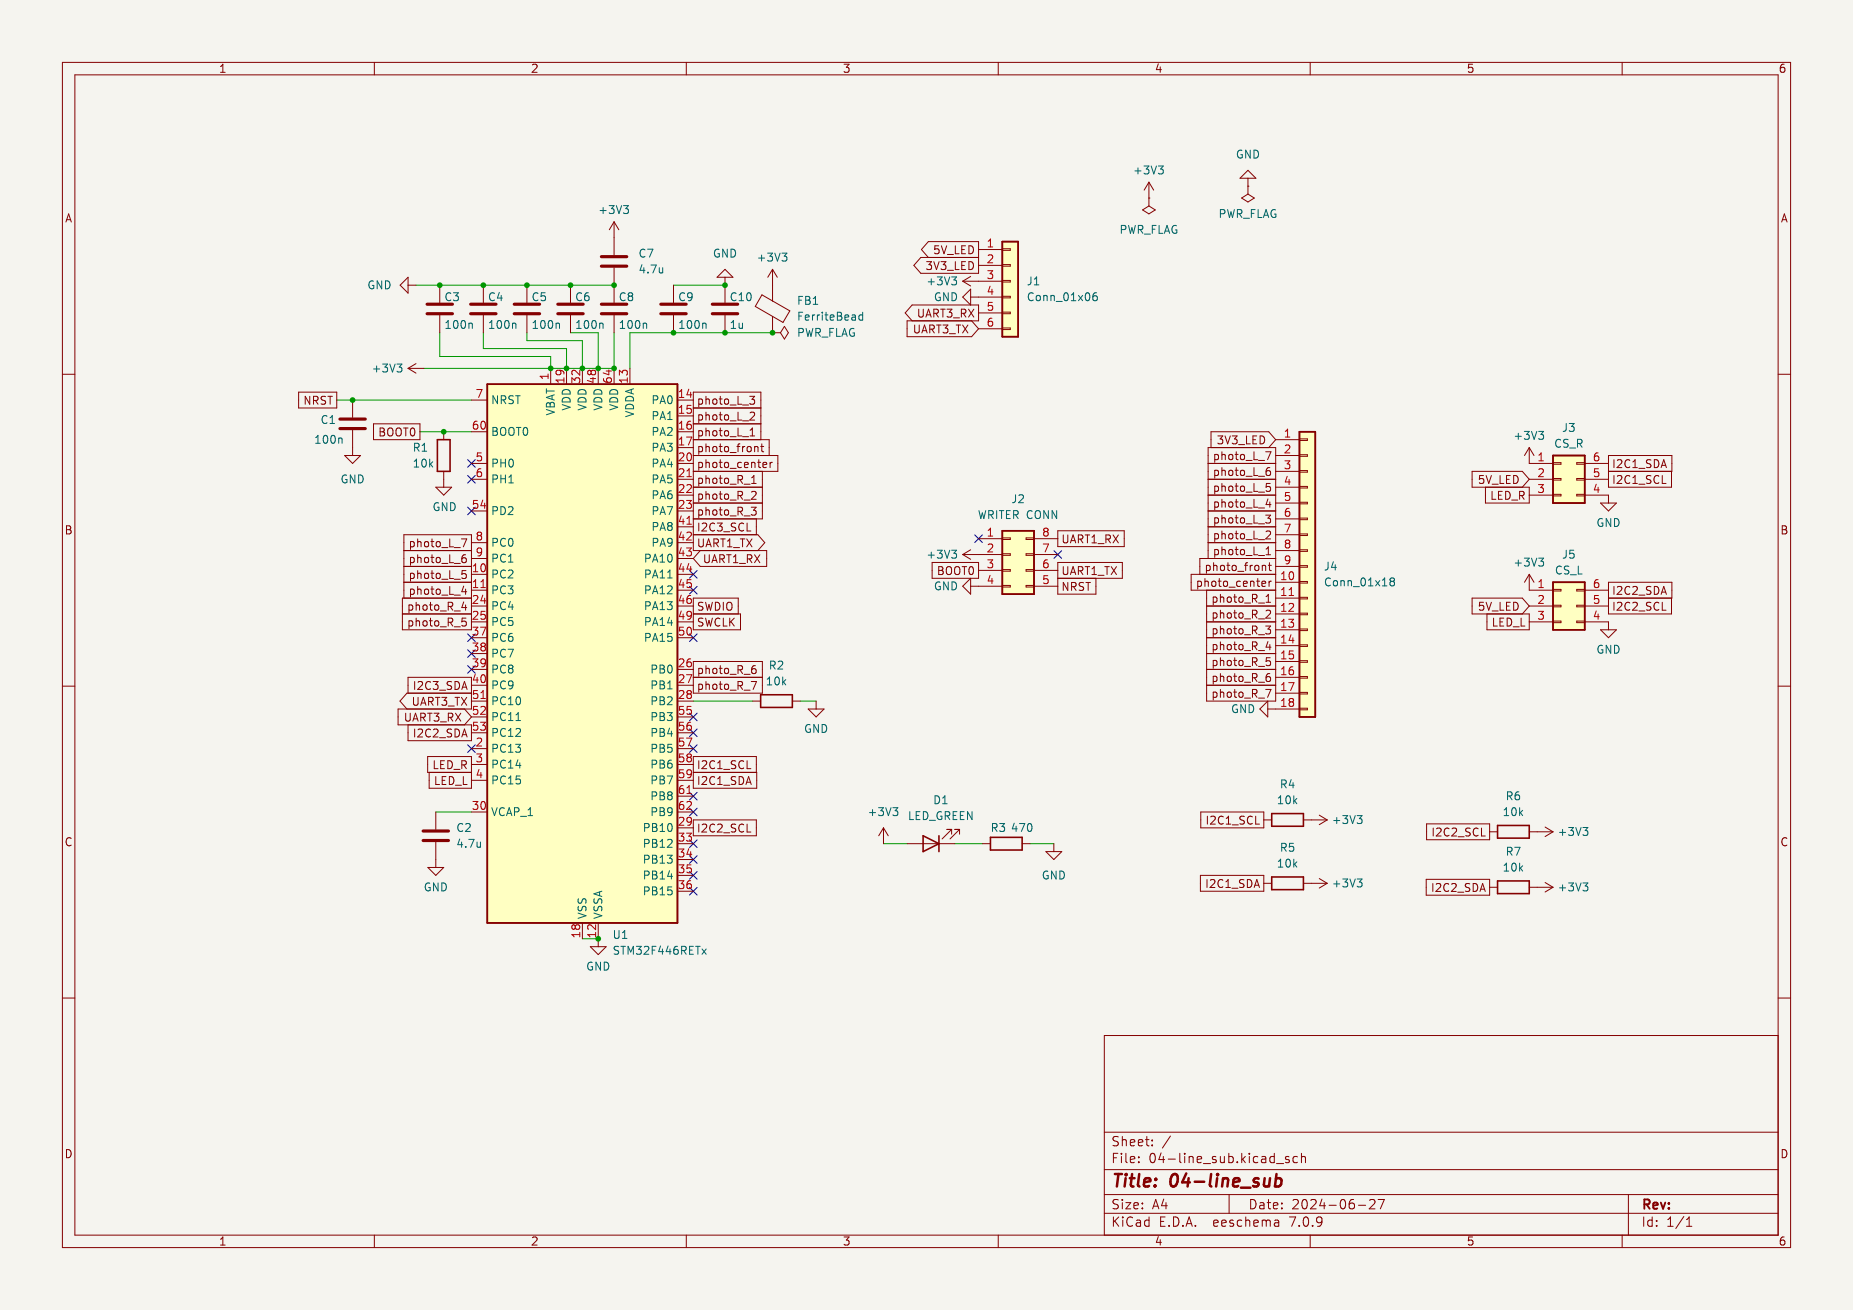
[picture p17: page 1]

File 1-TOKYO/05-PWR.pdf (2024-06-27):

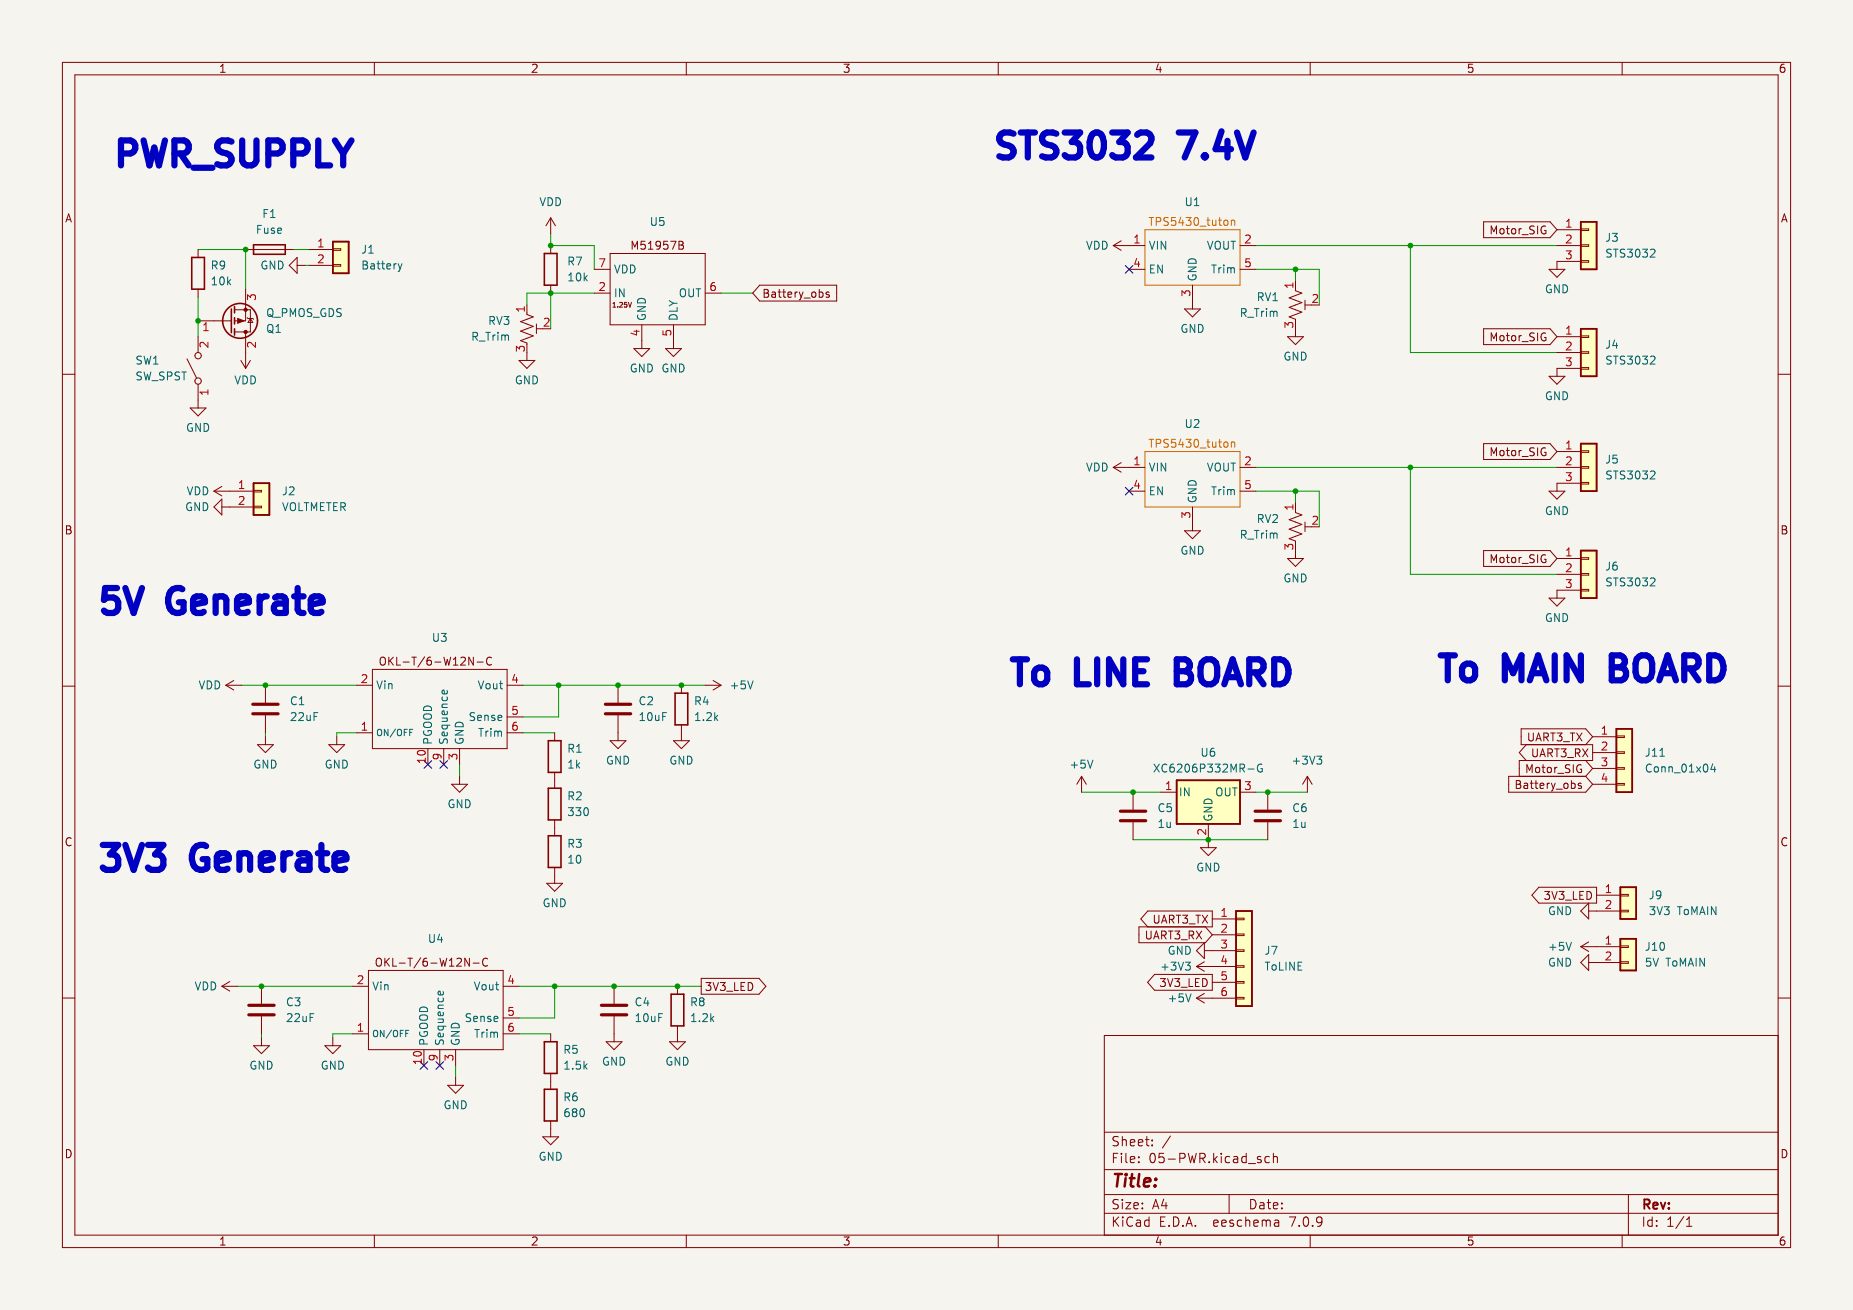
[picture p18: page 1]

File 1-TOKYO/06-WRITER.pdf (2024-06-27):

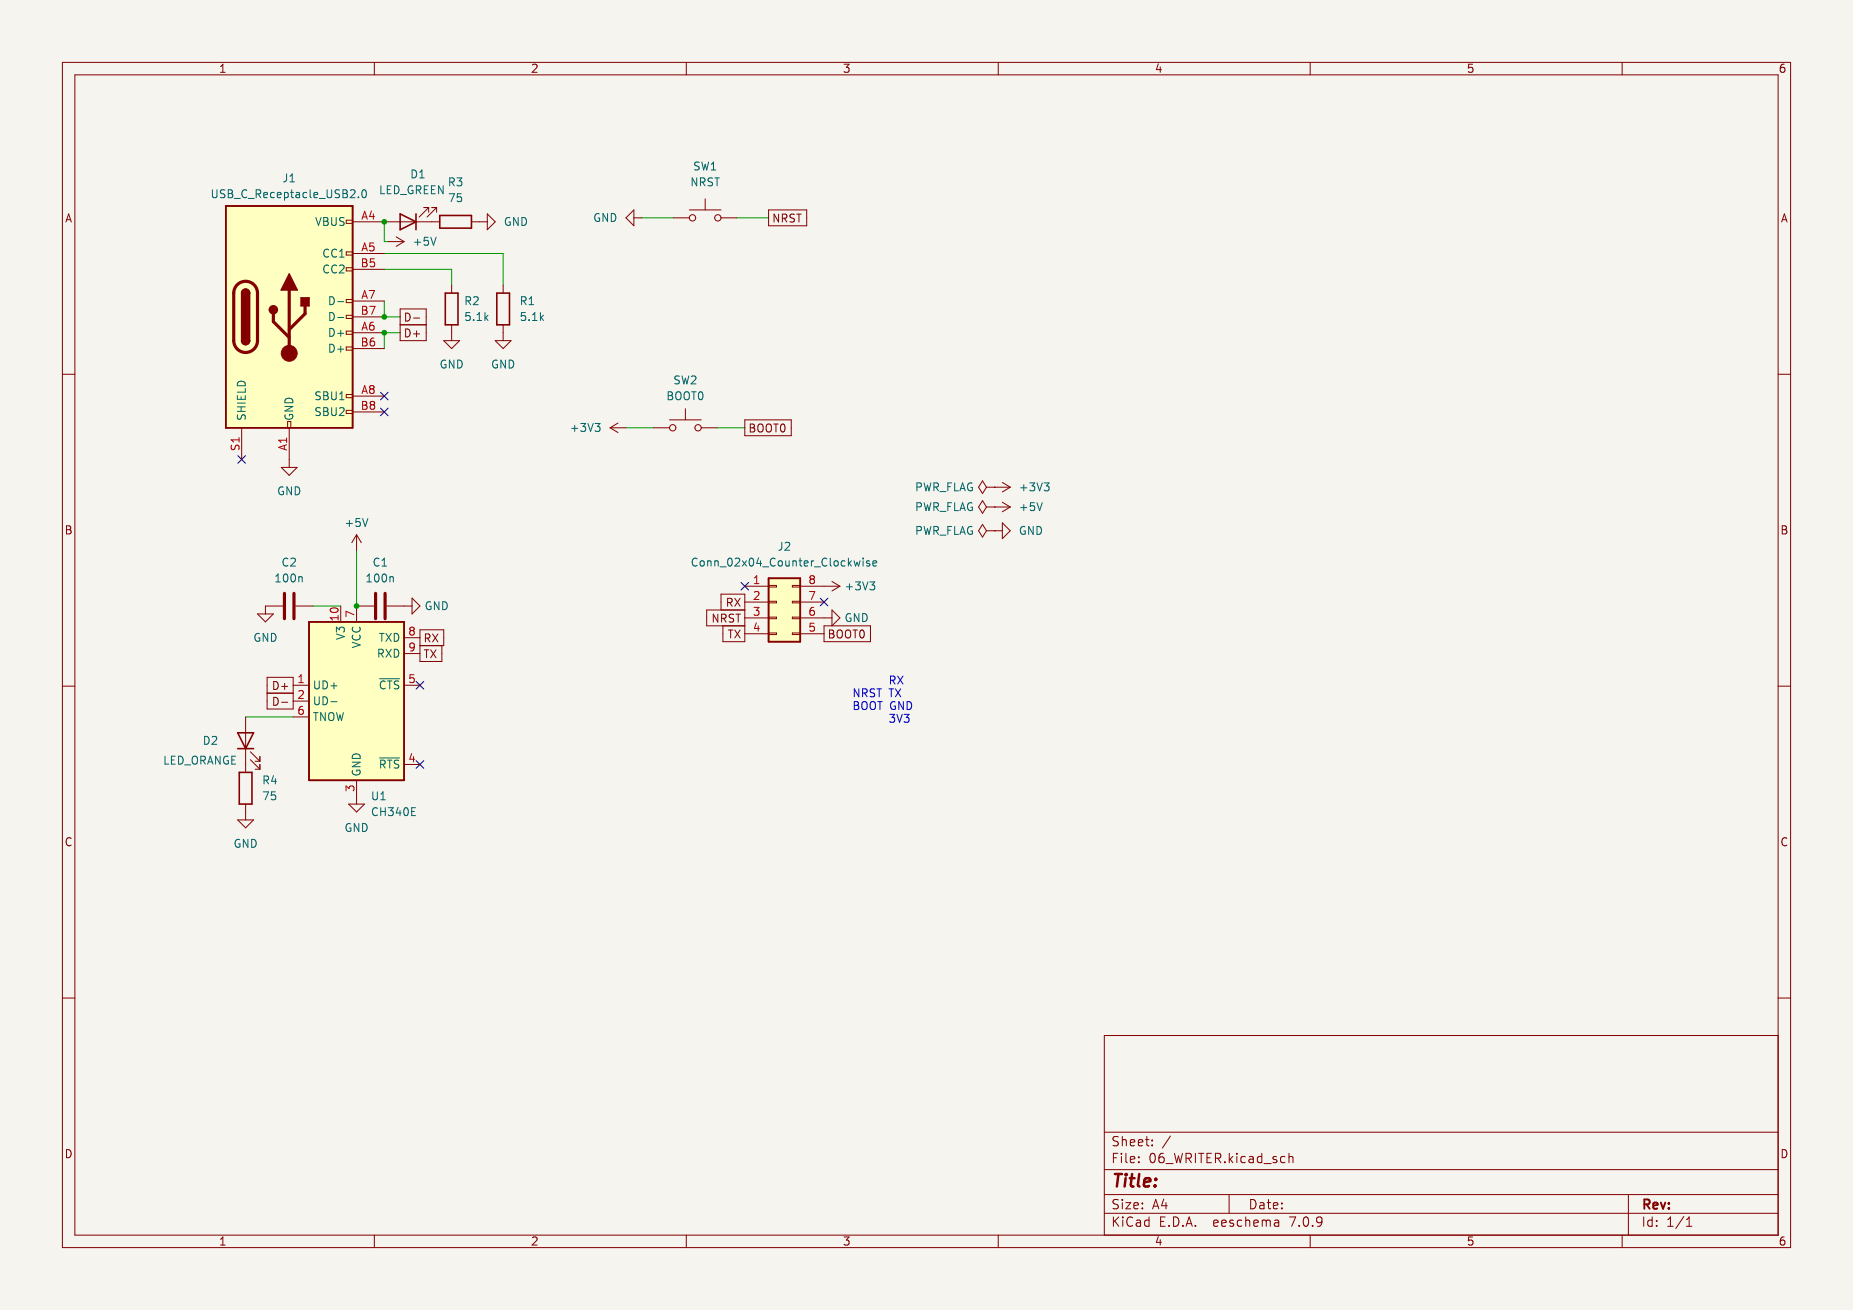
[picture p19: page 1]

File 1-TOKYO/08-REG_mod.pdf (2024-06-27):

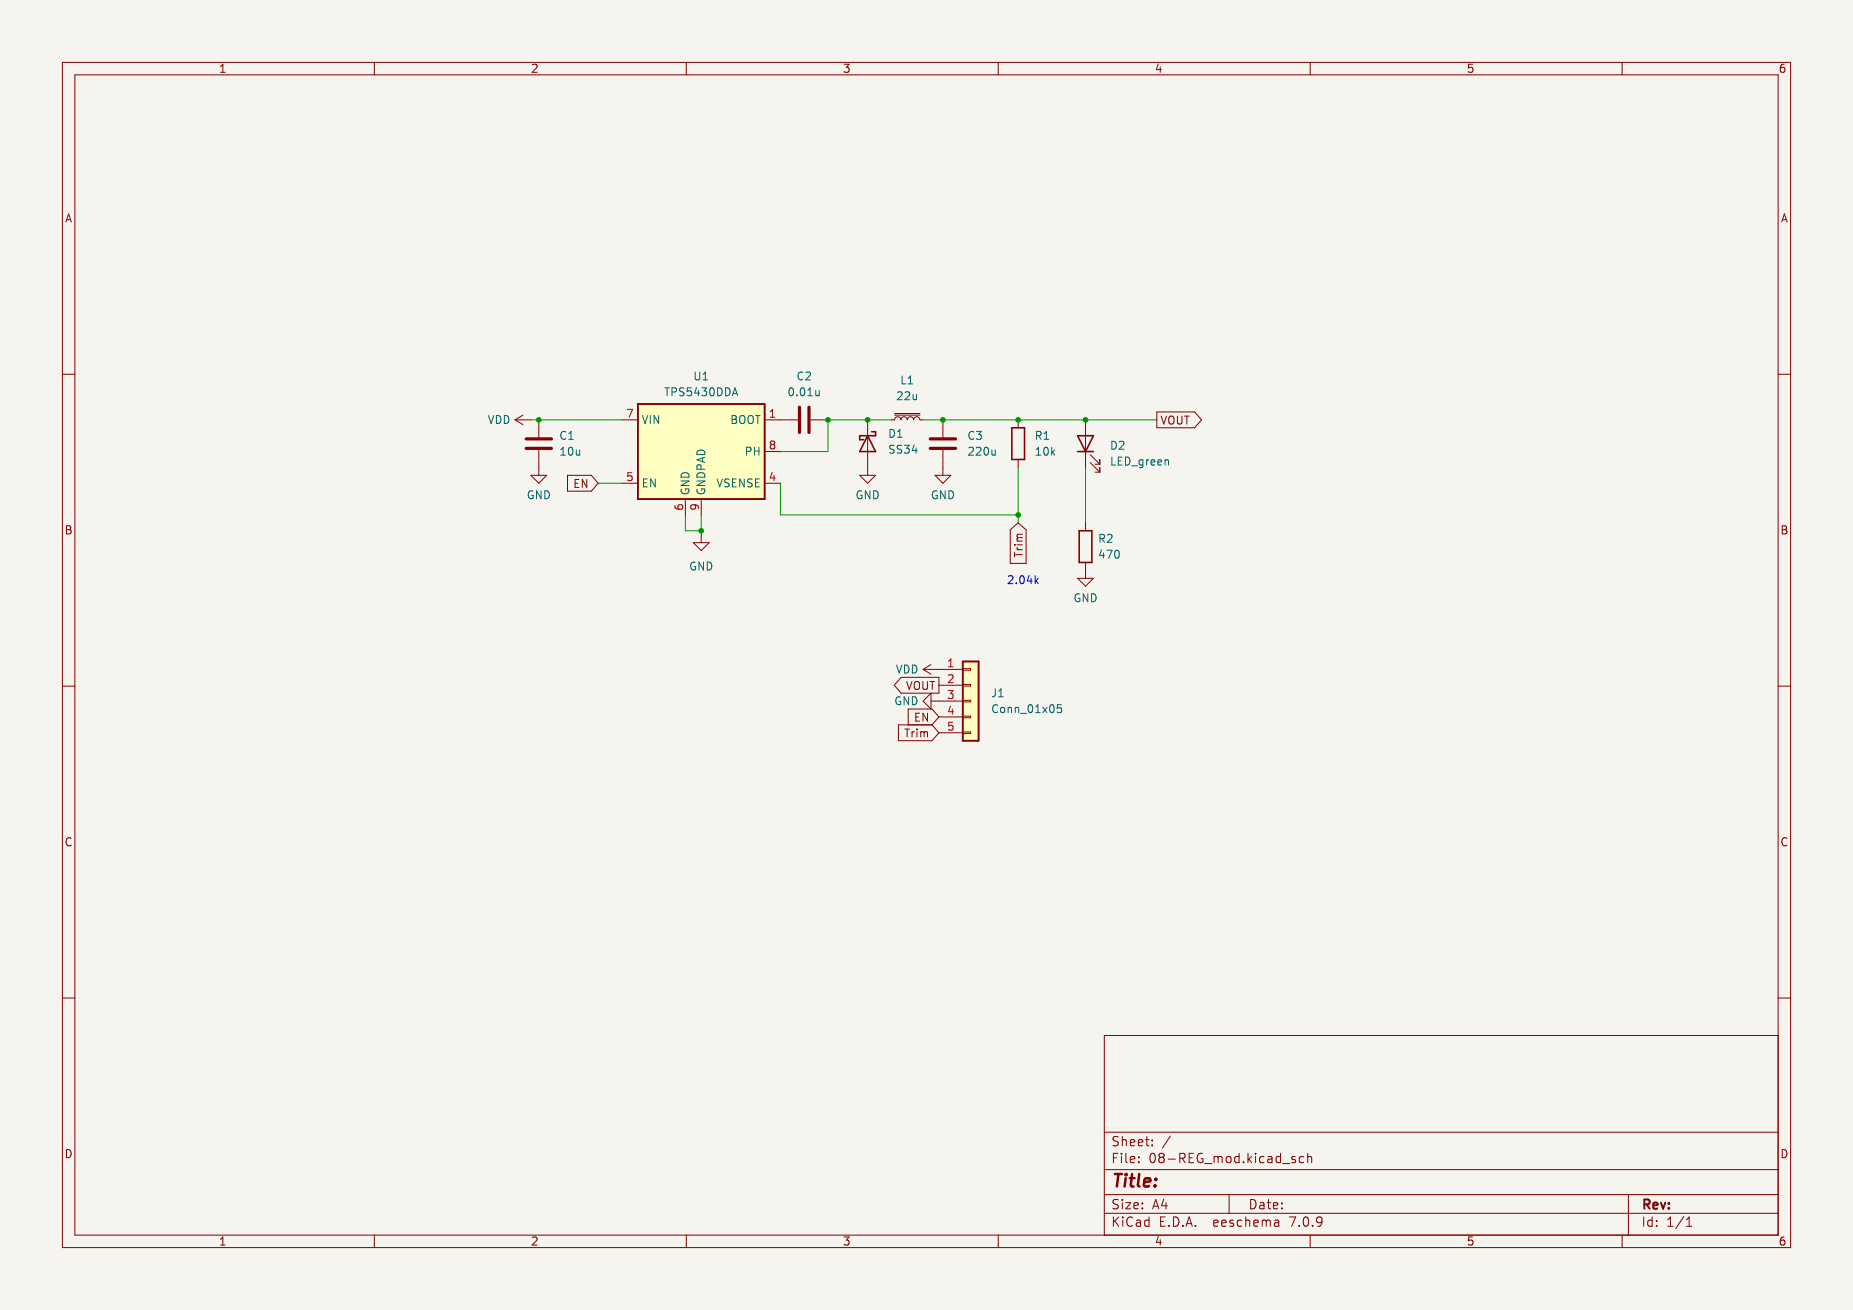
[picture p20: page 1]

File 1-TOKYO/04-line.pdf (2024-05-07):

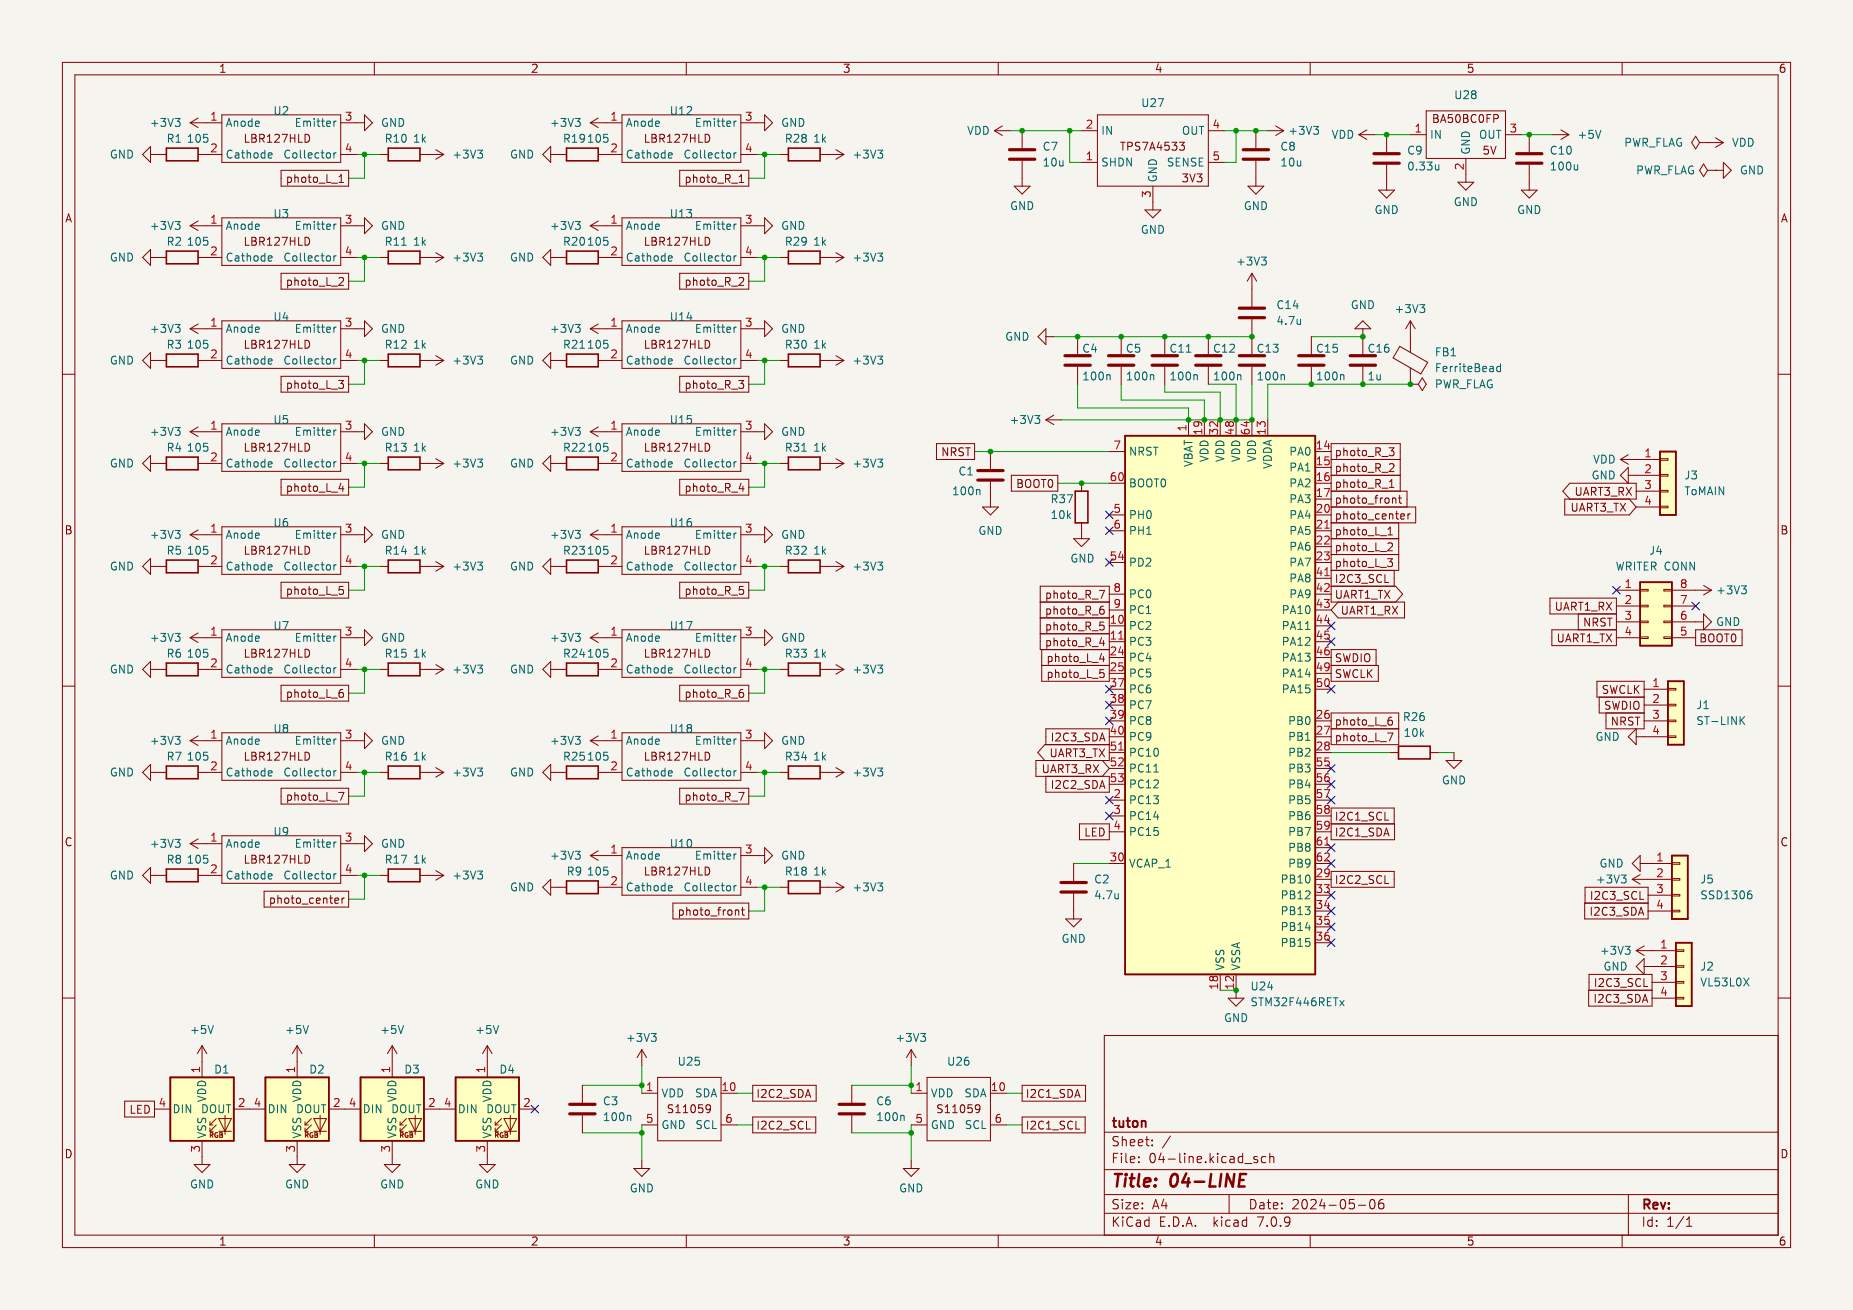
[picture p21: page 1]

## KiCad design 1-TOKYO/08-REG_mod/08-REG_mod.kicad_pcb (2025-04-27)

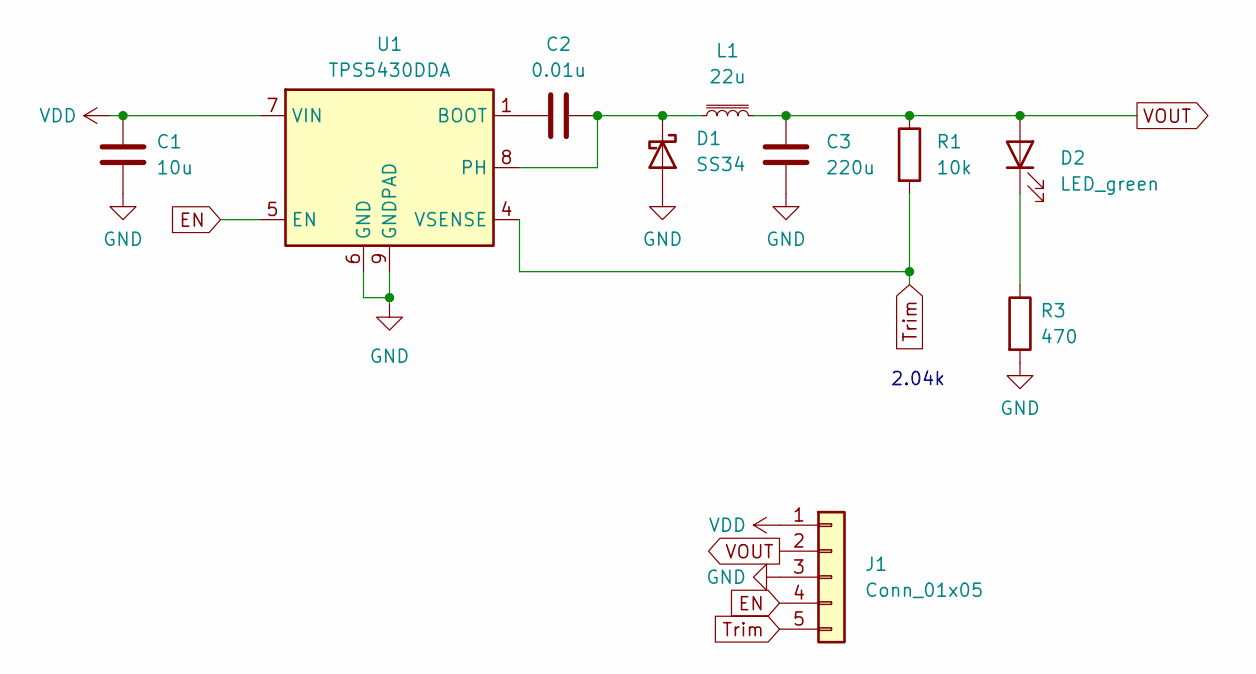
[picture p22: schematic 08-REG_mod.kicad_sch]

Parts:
C1: 10u; C_0805_2012Metric; LCSC C15850
C2: 0.01u; C_0603_1608Metric; LCSC C57112
C3: 220u; CP_Radial_D6.3mm_P2.50mm
D1: SS34; D_SMA; LCSC C8678
D2: LED_green; LED_0805_2012Metric; LCSC C2297
J1: Conn_01x05; PinHeader_1x05_P2.54mm_Horizontal
L1: 22u; FXL1040-220-M; LCSC C475917
R1: 10k; R_0603_1608Metric; LCSC C25804
R3: 470; R_0603_1608Metric; LCSC C23179
U1: TPS5430DDA; TI_SO-PowerPAD-8_ThermalVias

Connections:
EN: J1.4, U1.5 (EN)
GND: C1.2, C3.2, D1.2 (A), J1.3, U1.6 (GND), U1.9 (GNDPAD); also elsewhere on the board
unnamed: C2.2, D1.1 (K), L1.1, U1.8 (PH)
unnamed 3: D2.1 (K); also elsewhere on the board
unnamed: C2.1, U1.1 (BOOT)
Trim: J1.5, R1.2, U1.4 (VSENSE)
VDD: C1.1, J1.1, U1.7 (VIN)
VOUT: C3.1, D2.2 (A), J1.2, L1.2, R1.1

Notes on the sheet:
2.04k

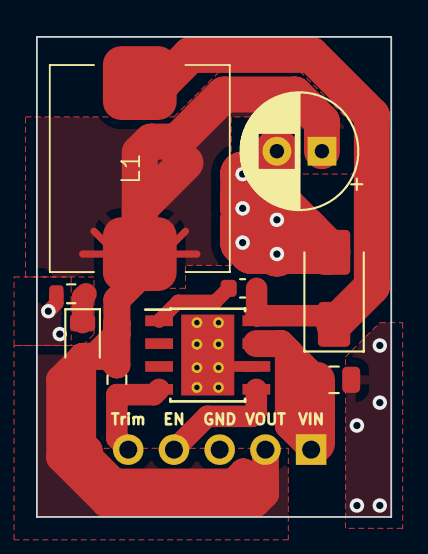
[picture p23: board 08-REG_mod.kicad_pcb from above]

Board: 2 copper layers, 19.7 x 26.7 mm, 10 parts (1 on the bottom side), 8 nets.

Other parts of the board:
R2: 470; R_0603_1608Metric

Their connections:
GND: R2.2; also elsewhere on the board
unnamed 3: R2.1; also elsewhere on the board

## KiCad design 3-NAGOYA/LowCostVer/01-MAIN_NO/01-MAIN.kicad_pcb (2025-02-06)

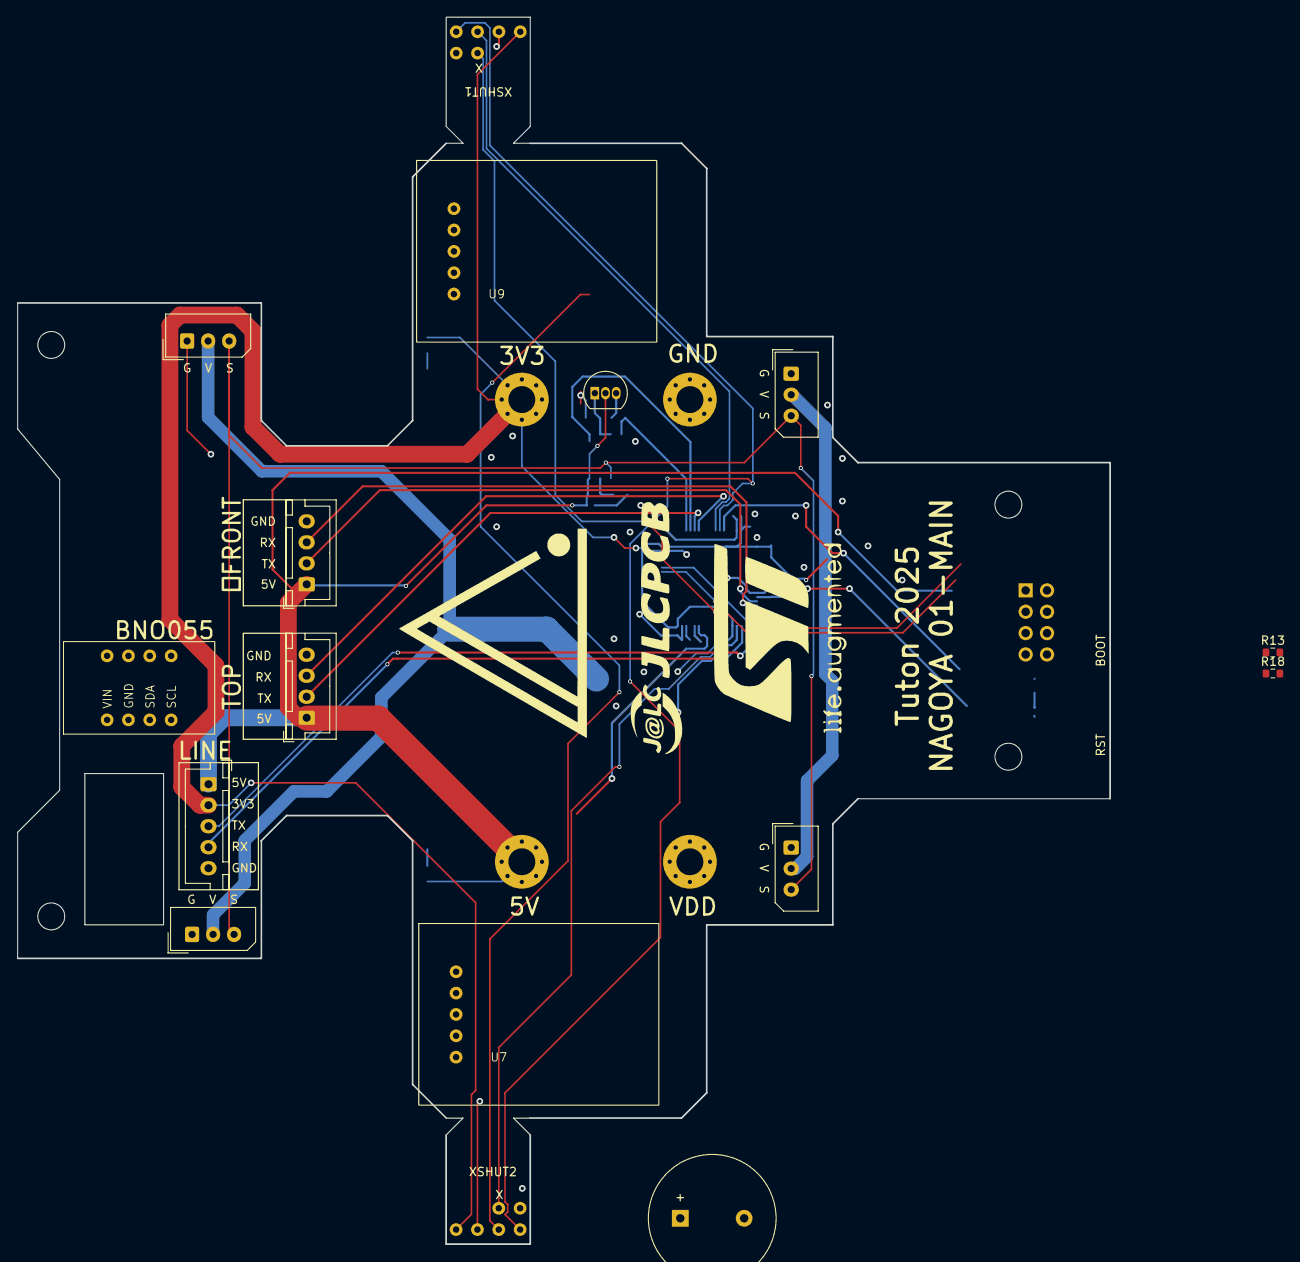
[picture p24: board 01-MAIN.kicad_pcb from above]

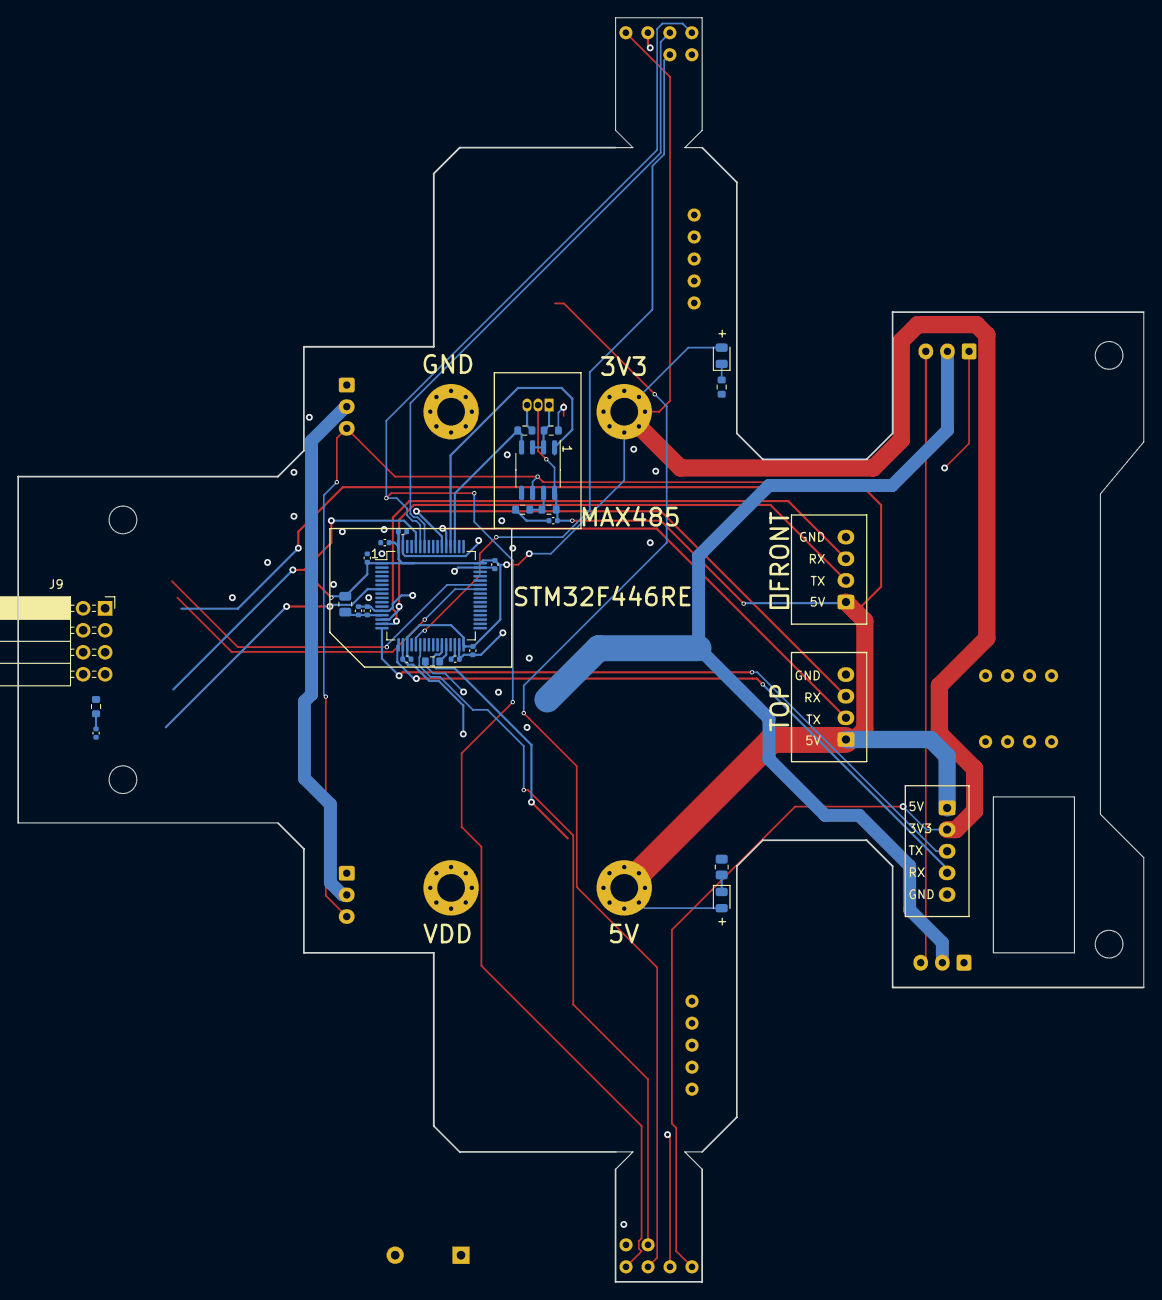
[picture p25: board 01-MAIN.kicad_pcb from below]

Board: 2 copper layers, 130.0 x 146.0 mm, 45 parts (25 on the bottom side), 34 nets.

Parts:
BZ1: Buzzer; Buzzer_15x7.5RM7.6
C1, C3, C4, C5, C6, C8, C9, C10: 100n; C_0402_1005Metric
C2, C7: 4.7u; C_0402_1005Metric
C11: 1u; C_0402_1005Metric
D1, D2: LED_GREEN; LED_0805_2012Metric
FB1: FerriteBead; R_0805_2012Metric
H1: ToMainVDD; MountingHole_3.2mm_M3_Pad_Via
H2: ToMainGND; MountingHole_3.2mm_M3_Pad_Via
H3: ToMain3V3; MountingHole_3.2mm_M3_Pad_Via
H4: ToMain5V; MountingHole_3.2mm_M3_Pad_Via
J1: Front; JST_XH_B4B-XH-A_1x04_P2.50mm_Vertical
J2: Top; JST_XH_B4B-XH-A_1x04_P2.50mm_Vertical
J3: toLINE; JST_XH_B5B-XH-A_1x05_P2.50mm_Vertical
J5, J6, J7, J8: STS3032; Molex_SPOX_5267-03A_1x03_P2.50mm_Vertical
J9: WRITER CONN; PinSocket_2x04_P2.54mm_Horizontal
Q1: 2SA1015; TO-92_Inline
R1: 7.5k; R_0603_1608Metric
R2, R6: 10k; R_0603_1608Metric
R3: 20k; R_0603_1608Metric
R4, R5, R13, R18: 2.2k; R_0603_1608Metric
R7: 470; R_0603_1608Metric
R8: 1k; R_0805_2012Metric
U1: STM32F446RETx; LQFP-64_10x10mm_P0.5mm
U2: MAX485ESA; SOP-8_3.9x4.9mm_P1.27mm
U3, U5: vl53l0x_vertical
U4: BNO055
U7, U9: TPS5430_horizontal

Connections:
+3V3: C3.2, C4.2, C5.2, C6.2, C7.1, C8.2, D1.2 (A), FB1.1, H3.1, J3.2, J9.1, U1.1 (VBAT), U1.19 (VDD), U1.32 (VDD), U1.48 (VDD), U1.64 (VDD), U3.1 (3V3), U4.1 (VIN), U5.1 (3V3)
+5V: C9.1, D2.2 (A), H4.1, J1.1, J2.1, J3.1, Q1.2 (C), R4.1, U2.8 (VCC)
BOOT0: J9.4, R2.1, U1.60 (BOOT0)
GND: BZ1.2 (+), C1.1, C2.2, C3.1, C4.1, C5.1, C6.1, C7.2, C8.1, C9.2, C10.1, C11.1, H2.1, J1.4, J2.4, J3.5, J5.1, J6.1, J7.1, J8.1, J9.3, R2.2, R3.2, R5.1, R6.2, R7.1, R8.1, R13.2, R18.2, U1.12 (VSSA), U1.18 (VSS), U1.31 (VSS), U1.47 (VSS), U1.63 (VSS), U2.5 (GND), U3.2 (GND), U4.2 (GND), U5.2 (GND), U7.3 (GND), U9.3 (GND)
I2C1_SCL: U1.58 (PB6), U3.3 (SCL), U4.4 (SCL), U5.3 (SCL)
I2C1_SDA: U1.59 (PB7), U3.4 (SDA), U4.3 (SDA), U5.4 (SDA)
NRST: C1.2, J9.6, U1.7 (NRST)
unnamed: D1.1 (K), R7.2
unnamed: D2.1 (K), R8.2
unnamed: J5.2, J6.2, U7.2 (VOUT)
unnamed: J7.2, J8.2, U9.2 (VOUT)
unnamed: Q1.3 (B), R1.1
unnamed: Q1.1 (E), R3.1, U2.2 (~RE), U2.3 (DE)
unnamed: R6.1, U1.28 (PB2)
unnamed: C2.1, U1.30 (VCAP_1)
unnamed: C10.2, C11.2, FB1.2, U1.13 (VDDA)
unnamed: R4.2, R5.2, U2.7 (B)
unnamed: R13.1, U7.5 (Trim)
unnamed: R18.1, U9.5 (Trim)
STS_SIG: J5.3, J6.3, J7.3, J8.3, U2.6 (A)
UART1_RX: J9.7, U1.43 (PA10)
UART1_TX: J9.5, U1.42 (PA9)
UART2_RX: J3.4, U1.17 (PA3)
UART2_TX: J3.3, U1.16 (PA2)
UART3_RX: U1.52 (PC11), U2.1 (RO)
UART3_TX: R1.2, U1.51 (PC10), U2.4 (DI)
UART4_RX: J1.3, U1.15 (PA1)
UART4_TX: J1.2, U1.14 (PA0)
UART5_RX: J2.3, U1.54 (PD2)
UART5_TX: J2.2, U1.53 (PC12)
VDD: H1.1, U7.1 (VIN), U9.1 (VIN)
XSHUT1: U1.21 (PA5), U3.5 (XSHUT)
XSHUT2: U1.22 (PA6), U5.5 (XSHUT)
buzzer: BZ1.1 (-), U1.27 (PB1)

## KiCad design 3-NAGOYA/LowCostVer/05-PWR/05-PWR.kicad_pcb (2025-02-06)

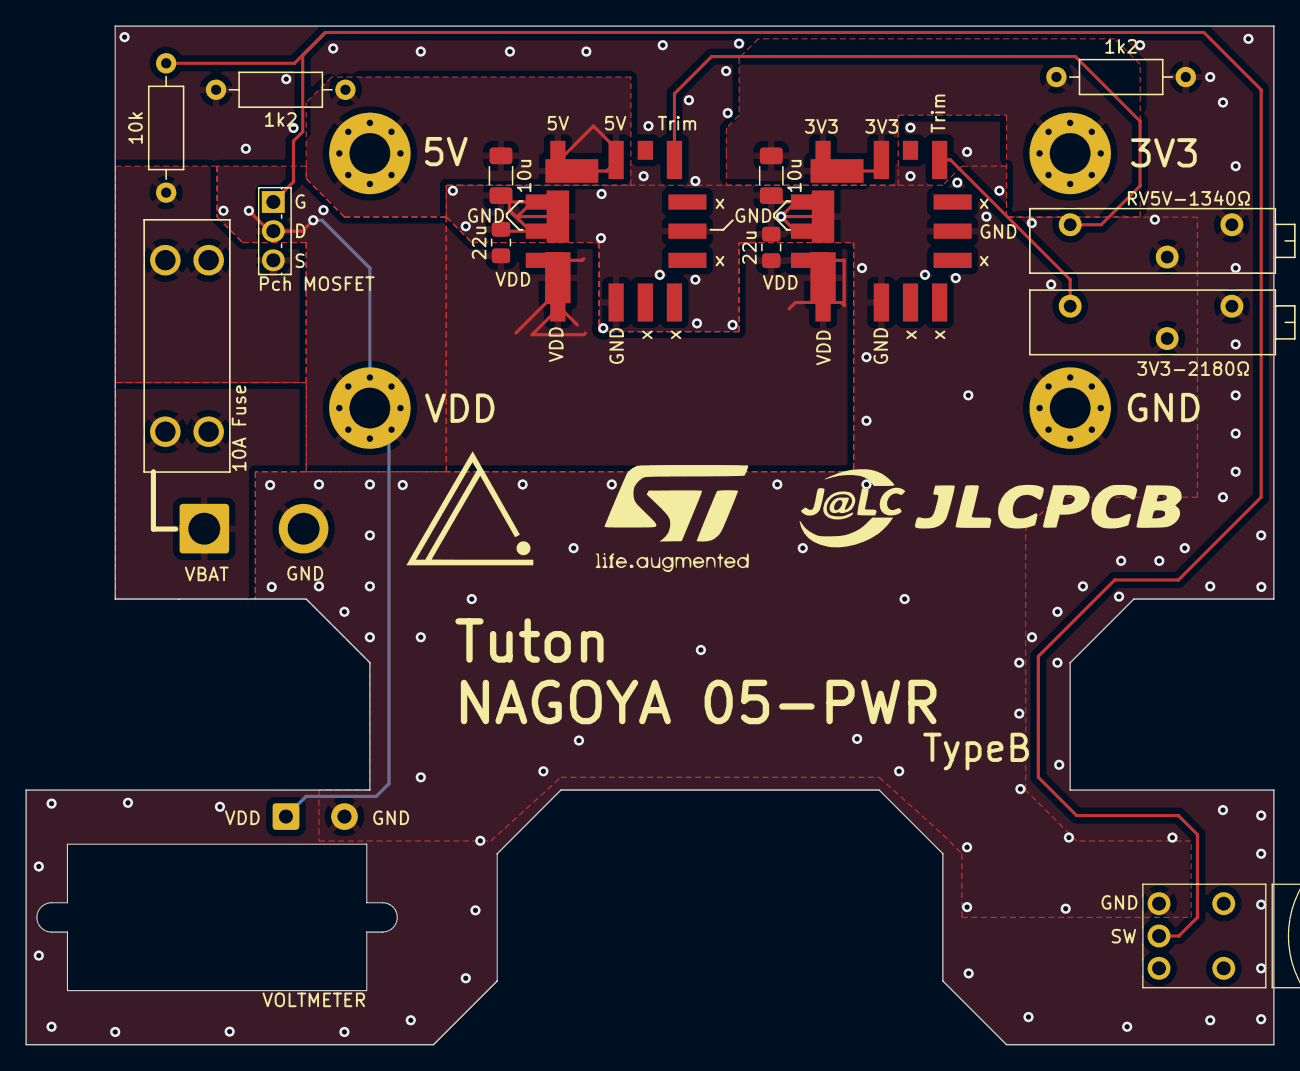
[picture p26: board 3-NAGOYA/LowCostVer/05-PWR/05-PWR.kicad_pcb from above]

Board: 2 copper layers, 98.0 x 80.0 mm, 20 parts (0 on the bottom side), 9 nets.

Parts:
1k2, 1k2#2: 1.2k; R_Axial_DIN0207_L6.3mm_D2.5mm_P10.16mm_Horizontal
3V3-2180Ω: 3kΩ; Potentiometer_Bourns_3006P_Horizontal
10k: 10k; R_Axial_DIN0207_L6.3mm_D2.5mm_P10.16mm_Horizontal
10u, 10u#2: 10uF; C_1206_3216Metric_Pad1.33x1.80mm_HandSolder
22u, 22u#2: 22uF; C_0805_2012Metric_Pad1.18x1.45mm_HandSolder
F1: Fuse; FUSE_3557-15
H1: ToMainVDD; MountingHole_3.2mm_M3_Pad_Via
H2: ToMainGND; MountingHole_3.2mm_M3_Pad_Via
H3: ToMain3V3; MountingHole_3.2mm_M3_Pad_Via
H4: ToMain5V; MountingHole_3.2mm_M3_Pad_Via
J1: voltmeter; SolderWire-0.5sqmm_1x02_P4.6mm_D0.9mm_OD2.1mm
J2: Battery; SolderWire-2sqmm_1x02_P7.8mm_D2mm_OD3.9mm
Q1: Q_PMOS_GDS; TO-251-3_Vertical
RV5V-1340Ω: 3kΩ; Potentiometer_Bourns_3006P_Horizontal
SW1: SW_SPST; AkizukiSmallRockerSwitchHorizontal
U1, U2: OKL-T6-W12N-C-SMD

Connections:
+3V3: 1k2.1, 10u#2.1, H3.1, U1.4 (Vout), U1.5 (Sense)
+5V: 1k2#2.1, 10u.1, H4.1, U2.4 (Vout), U2.5 (Sense)
GND: 1k2.2, 1k2#2.2, 3V3-2180Ω.2, 3V3-2180Ω.3, 10u.2, 10u#2.2, 22u.2, 22u#2.2, H2.1, J1.2, J2.2, RV5V-1340Ω.2, RV5V-1340Ω.3, SW1.1 (A), U1.1 (ON/OFF), U1.3 (GND), U1.7 (GND), U2.1 (ON/OFF), U2.3 (GND), U2.7 (GND)
unnamed: F1.2, J2.1
unnamed: 10k.2, Q1.1 (G), SW1.2 (B)
unnamed: 10k.1, F1.1, Q1.3 (S)
unnamed: 3V3-2180Ω.1, U1.6 (Trim)
unnamed: RV5V-1340Ω.1, U2.6 (Trim)
VDD: 22u.1, 22u#2.1, H1.1, J1.1, Q1.2 (D), U1.2 (Vin), U2.2 (Vin)

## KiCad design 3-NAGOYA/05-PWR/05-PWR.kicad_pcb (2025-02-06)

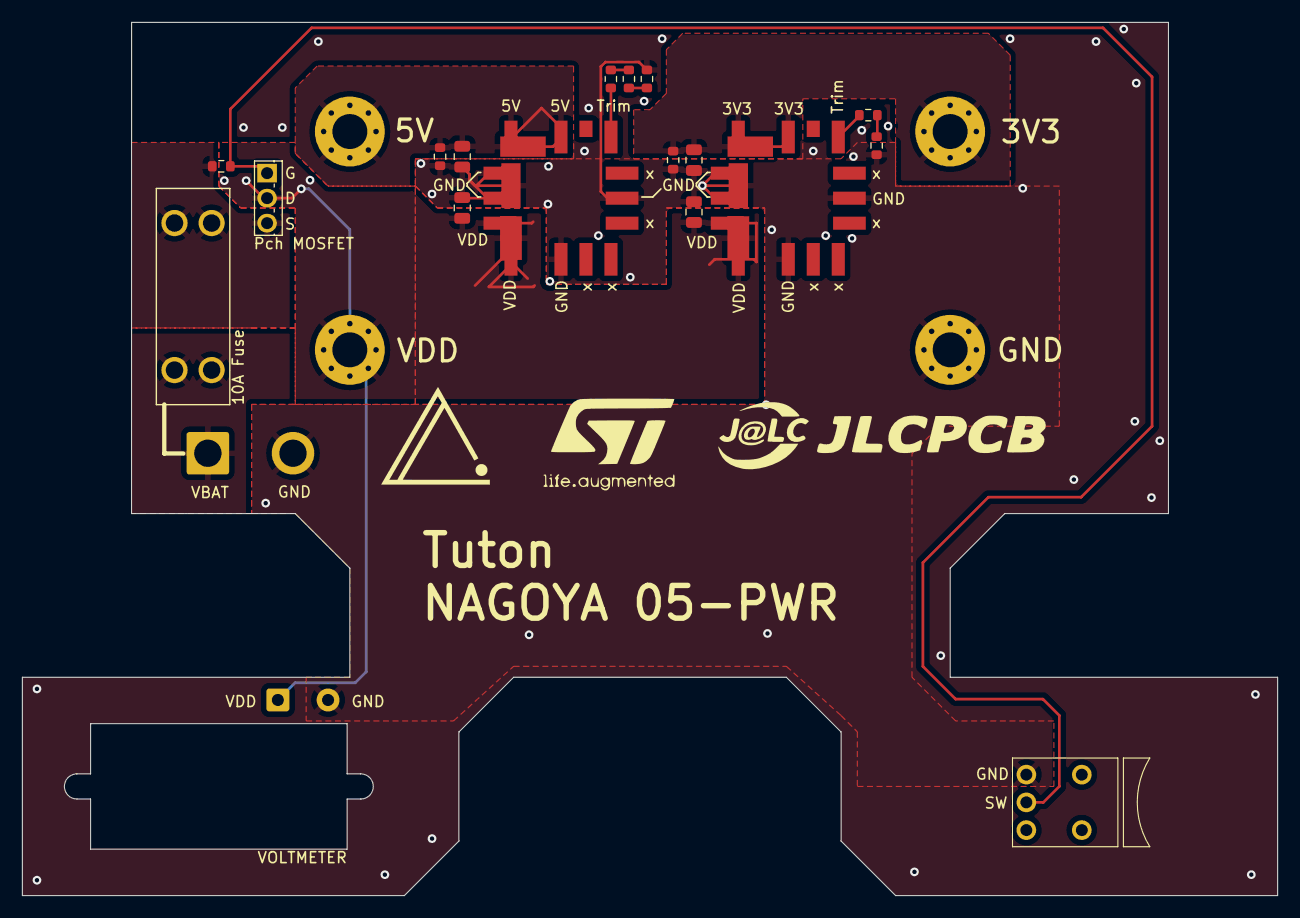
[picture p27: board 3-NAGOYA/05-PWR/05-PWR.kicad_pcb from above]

Board: 2 copper layers, 115.0 x 80.0 mm, 23 parts (0 on the bottom side), 12 nets.

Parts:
C1, C2: 22uF; C_0805_2012Metric
C3, C4: 10uF; C_0805_2012Metric
F1: Fuse; FUSE_3557-15
H1: ToMainVDD; MountingHole_3.2mm_M3_Pad_Via
H2: ToMainGND; MountingHole_3.2mm_M3_Pad_Via
H3: ToMain3V3; MountingHole_3.2mm_M3_Pad_Via
H4: ToMain5V; MountingHole_3.2mm_M3_Pad_Via
J1: voltmeter; SolderWire-0.5sqmm_1x02_P4.6mm_D0.9mm_OD2.1mm
J2: Battery; SolderWire-2sqmm_1x02_P7.8mm_D2mm_OD3.9mm
Q1: Q_PMOS_GDS; TO-251-3_Vertical
R1: 1k; R_0603_1608Metric
R2: 330; R_0603_1608Metric
R3: 10; R_0603_1608Metric
R4: 1.5k; R_0603_1608Metric
R5: 680; R_0603_1608Metric
R6, R7: 1.2k; R_0603_1608Metric
R8: 10k; R_0603_1608Metric
SW1: SW_SPST; AkizukiSmallRockerSwitchHorizontal
U1, U2: OKL-T6-W12N-C-SMD

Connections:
+3V3: C3.1, H3.1, R6.1, U1.4 (Vout), U1.5 (Sense)
+5V: C4.1, H4.1, R7.1, U2.4 (Vout), U2.5 (Sense)
GND: C1.2, C2.2, C3.2, C4.2, H2.1, J1.2, J2.2, R3.2, R5.2, R6.2, R7.2, SW1.1 (A), U1.1 (ON/OFF), U1.3 (GND), U1.7 (GND), U2.1 (ON/OFF), U2.3 (GND), U2.7 (GND)
unnamed: F1.2, J2.1
unnamed: Q1.1 (G), R8.2, SW1.2 (B)
unnamed: F1.1, Q1.3 (S), R8.1
unnamed: R1.2, R2.1
unnamed: R2.2, R3.1
unnamed: R4.2, R5.1
unnamed: R4.1, U1.6 (Trim)
unnamed: R1.1, U2.6 (Trim)
VDD: C1.1, C2.1, H1.1, J1.1, Q1.2 (D), U1.2 (Vin), U2.2 (Vin)

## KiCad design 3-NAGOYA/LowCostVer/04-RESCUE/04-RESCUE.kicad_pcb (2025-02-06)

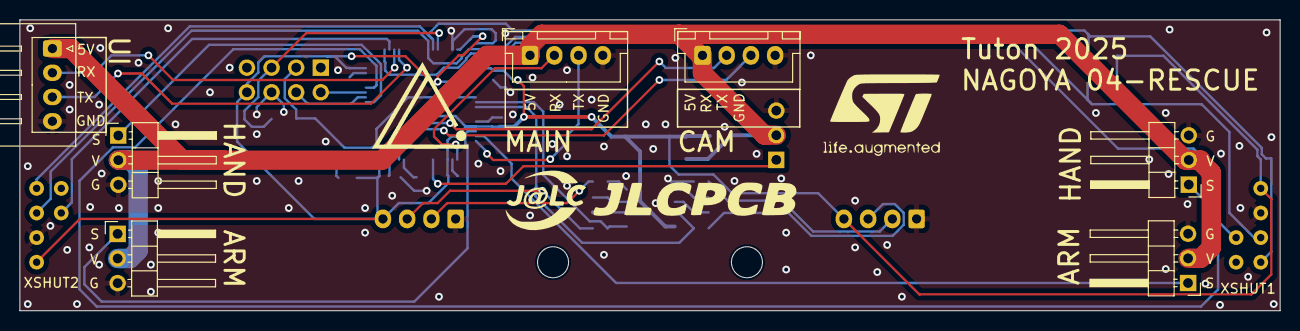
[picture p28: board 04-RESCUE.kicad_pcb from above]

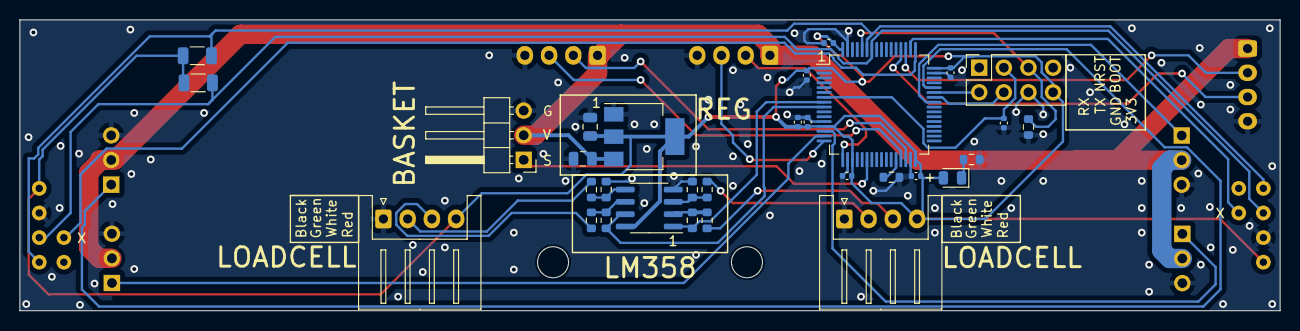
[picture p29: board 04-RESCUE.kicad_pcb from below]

Board: 2 copper layers, 130.0 x 30.0 mm, 40 parts (33 on the bottom side), 34 nets.

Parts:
C1, C2: 22u; C_0805_2012Metric
C8, C9, C10, C11, C12, C14, C15: 100n; C_0402_1005Metric
C13: 4.7u; C_0402_1005Metric
D1: LED_GREEN; LED_0805_2012Metric
J1: UI; JST_XH_S4B-XH-A_1x04_P2.50mm_Horizontal
J2: MAIN; JST_XH_B4B-XH-A_1x04_P2.50mm_Vertical
J3: LOADCELL_R; JST_XH_S4B-XH-A_1x04_P2.50mm_Horizontal
J4: WRITER CONN; PinSocket_2x04_P2.54mm_Vertical
J5: LOADCELL_L; JST_XH_S4B-XH-A_1x04_P2.50mm_Horizontal
J6: OpenMV; JST_XH_B4B-XH-A_1x04_P2.50mm_Vertical
M1: ServoBasketLeft; PinHeader_1x03_P2.54mm_Horizontal
M3: ServoArmLeft; PinHeader_1x03_P2.54mm_Horizontal
M4: ServoArmRight; PinHeader_1x03_P2.54mm_Horizontal
M5: ServoHandLeft; PinHeader_1x03_P2.54mm_Horizontal
M6: ServoHandRight; PinHeader_1x03_P2.54mm_Horizontal
R1, R2, R3, R6: 330; R_0603_1608Metric
R4, R5: 10k; R_0603_1608Metric
R7, R8, R9, R10: 1M; R_0603_1608Metric
R11: 470; R_0603_1608Metric
R12, R13: 10k; R_1206_3216Metric
U1: LM358; SOIC-8_3.9x4.9mm_P1.27mm
U2, U3: vl53l0x_vertical
U4: STM32F103RCTx; LQFP-64_10x10mm_P0.5mm
U5: AMS1117-3.3; SOT-223-3_TabPin2

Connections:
+3V3: C2.1, C8.2, C9.2, C10.2, C11.2, C12.2, C13.2, C14.2, D1.2 (A), J3.4, J4.8, J5.4, R12.1, R13.2, U1.8 (V+), U2.1 (3V3), U3.1 (3V3), U4.1 (VBAT), U4.13 (VDDA), U4.19 (VDD), U4.32 (VDD), U4.48 (VDD), U4.64 (VDD), U5.2 (VO)
+5V: C1.1, J1.1, J2.1, J6.1, M1.2 (+), M3.2 (+), M4.2 (+), M5.2 (+), M6.2 (+), U5.3 (VI)
BOOT0: J4.5, R4.1, U4.60 (BOOT0)
GND: C1.2, C2.2, C8.1, C9.1, C10.1, C11.1, C12.1, C13.1, C14.1, C15.1, J1.4, J2.4, J3.1, J4.6, J5.1, J6.4, M1.3 (-), M3.3 (-), M4.3 (-), M5.3 (-), M6.3 (-), R4.2, R5.1, R7.2, R9.2, R11.1, U1.4 (V-), U2.2 (GND), U3.2 (GND), U4.12 (VSSA), U4.18 (VSS), U4.31 (VSS), U4.47 (VSS), U4.63 (VSS), U5.1 (GND)
LOADCEL_L: R10.1, U1.1, U4.8 (PC0)
LOADCEL_R: R8.1, U1.7, U4.9 (PC1)
NRST: C15.2, J4.3, U4.7 (NRST)
unnamed: D1.1 (K), R11.2
unnamed: J3.2, R1.1
unnamed: J3.3, R2.2
unnamed: J5.2, R3.1
unnamed: J5.3, R6.2
unnamed: R3.2, R9.1, U1.3 (+)
unnamed: R6.1, R10.2, U1.2 (-)
unnamed: R1.2, R7.1, U1.5 (+)
unnamed: R2.1, R8.2, U1.6 (-)
unnamed: R5.2, U4.28 (PB2)
SCL: R13.1, U2.3 (SCL), U3.3 (SCL), U4.58 (PB6)
SDA: R12.2, U2.4 (SDA), U3.4 (SDA), U4.59 (PB7)
ServoArmLeft: M3.1 (PWM), U4.14 (PA0)
ServoArmRight: M4.1 (PWM), U4.15 (PA1)
ServoBasket: M1.1 (PWM), U4.22 (PA6)
ServoHandLeft: M5.1 (PWM), U4.41 (PA8)
ServoHandRight: M6.1 (PWM), U4.44 (PA11)
UART1_RX: J4.2, U4.43 (PA10)
UART1_TX: J4.4, U4.42 (PA9)
UART2_RX: J2.2, U4.17 (PA3)
UART2_TX: J2.3, U4.16 (PA2)
UART3_RX: J6.2, U4.30 (PB11)
UART3_TX: J6.3, U4.29 (PB10)
UART4_RX: J1.3, U4.52 (PC11)
UART4_TX: J1.2, U4.51 (PC10)
XSHUT1: U2.5 (XSHUT), U4.49 (PA14)
XSHUT2: U3.5 (XSHUT), U4.50 (PA15)

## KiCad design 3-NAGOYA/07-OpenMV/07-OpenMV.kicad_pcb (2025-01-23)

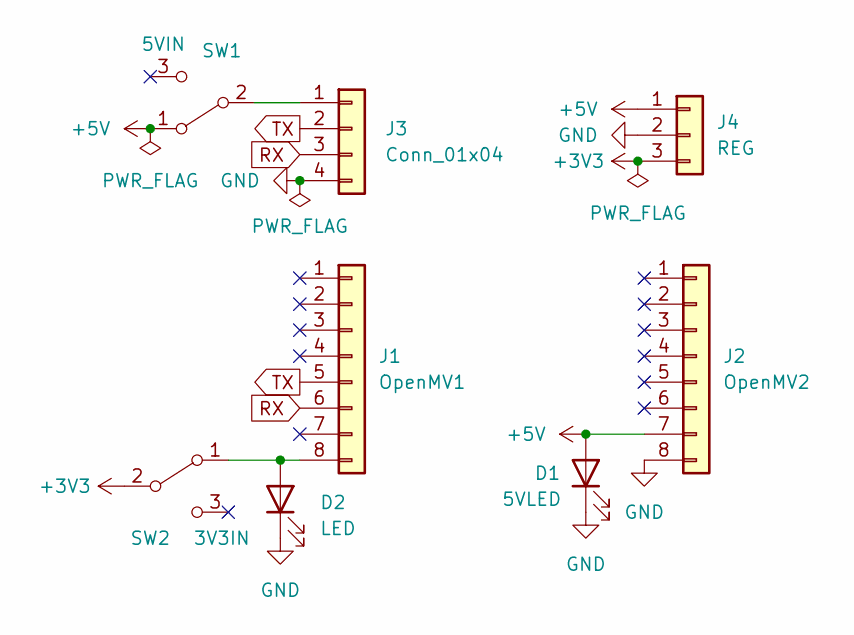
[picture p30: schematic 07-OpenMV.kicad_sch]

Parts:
D1: 5VLED; LED_D3.0mm_Clear
D2: LED; LED_D3.0mm_Clear
J1: OpenMV1; PinSocket_1x08_P2.54mm_Vertical
J2: OpenMV2; PinSocket_1x08_P2.54mm_Vertical
J3: Conn_01x04; JST_XH_S4B-XH-A_1x04_P2.50mm_Horizontal
J4: REG; PinHeader_1x03_P2.54mm_Vertical
SW1: 5VIN; SK-12D11VG3
SW2: 3V3IN; SK-12D11VG3

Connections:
+3V3: J4.3, SW2.2 (B)
+5V: D1.2 (A), J2.7, J4.1, SW1.1 (A)
GND: D1.1 (K), D2.1 (K), J2.8, J3.4, J4.2
unnamed: D2.2 (A), J1.8, SW2.1 (A)
unnamed: J3.1, SW1.2 (B)
RX: J1.6, J3.3
TX: J1.5, J3.2

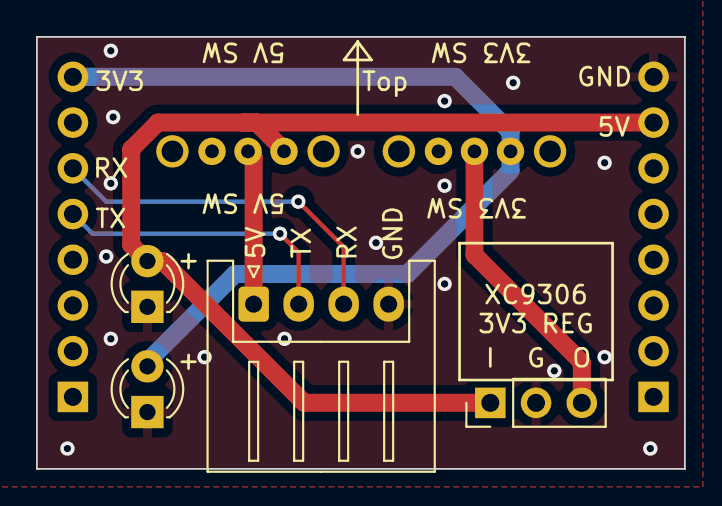
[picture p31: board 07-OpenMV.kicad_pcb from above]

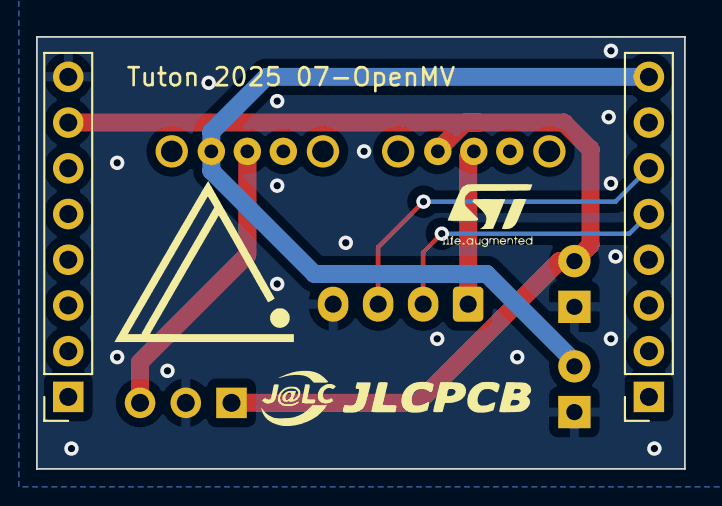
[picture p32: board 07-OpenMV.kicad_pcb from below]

Board: 2 copper layers, 36.0 x 24.0 mm, 8 parts (2 on the bottom side), 7 nets.

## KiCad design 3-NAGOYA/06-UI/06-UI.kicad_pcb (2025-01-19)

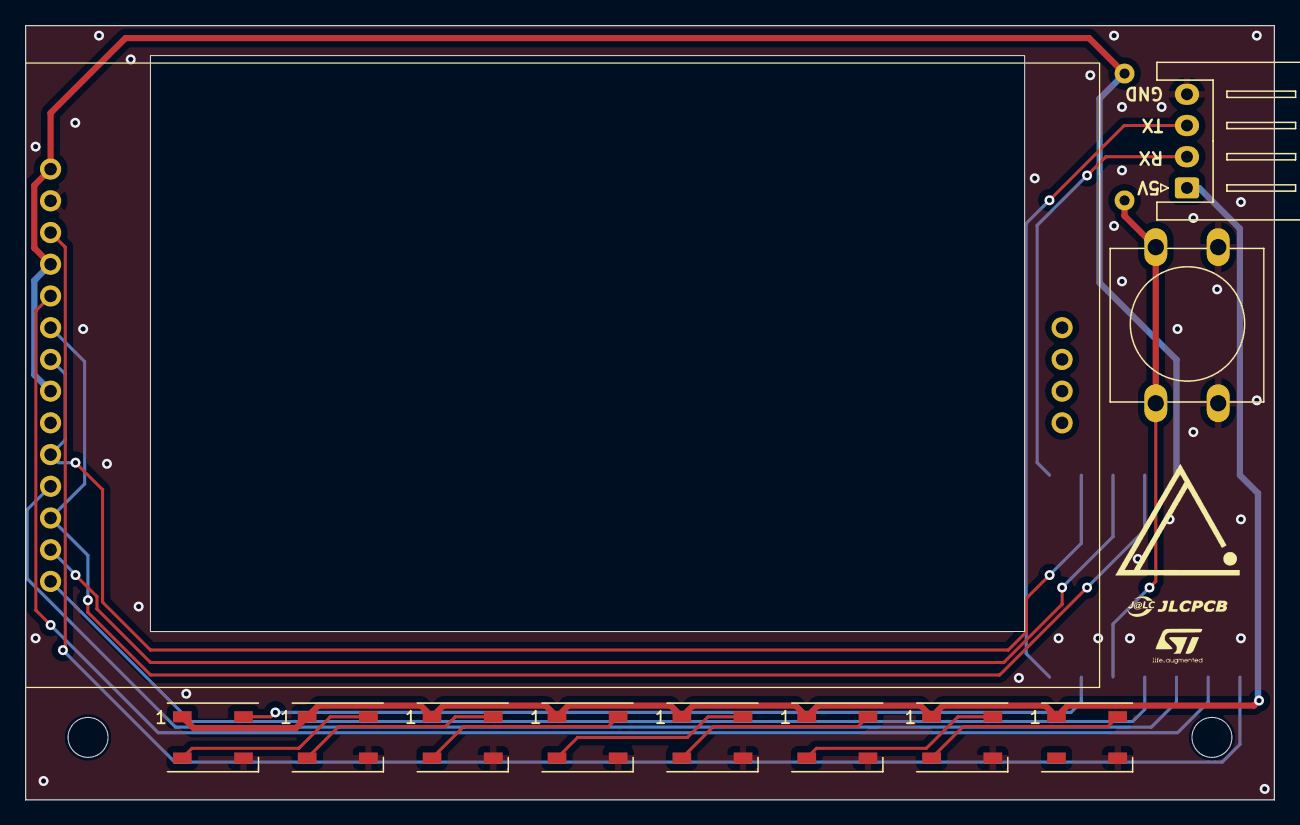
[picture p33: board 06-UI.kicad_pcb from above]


Board: 2 copper layers, 100.0 x 62.0 mm, 15 parts (2 on the bottom side), 21 nets.

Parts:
D1, D2, D3, D4, D5, D6, D7, D8: WS2812B; LED_WS2812B_PLCC4_5.0x5.0mm_P3.2mm
H1, H2: MountingHole; MountingHole_3.2mm_M3
J1: OpenMV Conn; JST_XH_S4B-XH-A_1x04_P2.50mm_Horizontal
R1: R; R_Axial_DIN0207_L6.3mm_D2.5mm_P10.16mm_Horizontal
SW1: SW_Push; SW_PUSH-12mm
U1: MOUDLE14P-SMD-2.54-21X17.8MM
U2: MS2807

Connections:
+3V3: R1.2, U1.12 (3V3), U2.1 (VCC), U2.4 (RESET), U2.8 (LED)
+5V: D1.1 (VDD), D2.1 (VDD), D3.1 (VDD), D4.1 (VDD), D5.1 (VDD), D6.1 (VDD), D7.1 (VDD), D8.1 (VDD), J1.1, U1.14 (5V)
Display_CS: U1.1 (D0/A0), U2.3 (CS)
Display_DC: U1.2 (D1/A1), U2.5 (DC/RS)
GND: D1.3 (VSS), D2.3 (VSS), D3.3 (VSS), D4.3 (VSS), D5.3 (VSS), D6.3 (VSS), D7.3 (VSS), D8.3 (VSS), J1.4, SW1.2, U1.13 (GND), U2.2 (GND)
MISO: U1.10 (D9), U2.13 (T_DOUT)
MOSI: U1.11 (D10), U2.6 (MOSI), U2.12 (T_DIN)
unnamed: D1.2 (DOUT), D2.4 (DIN)
unnamed: D2.2 (DOUT), D3.4 (DIN)
unnamed: D3.2 (DOUT), D4.4 (DIN)
unnamed: D4.2 (DOUT), D5.4 (DIN)
unnamed: D5.2 (DOUT), D6.4 (DIN)
unnamed: D6.2 (DOUT), D7.4 (DIN)
unnamed: D7.2 (DOUT), D8.4 (DIN)
RX: J1.2, U1.8 (RX/D7)
SCK: U1.9 (D8), U2.7 (SCK), U2.10 (T_CLK)
SW: R1.1, SW1.1, U1.5 (D4/SDA)
TX: J1.3, U1.7 (D6/TX)
Touch_CS: U1.3 (D2/A2), U2.11 (T_CS)
Touch_IRQ: U1.4 (D3/A3), U2.14 (T_IRQ)
WS2812B: D1.4 (DIN), U1.6 (D5/SCL)

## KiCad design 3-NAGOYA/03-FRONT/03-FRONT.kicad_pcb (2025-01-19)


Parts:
D1, D2, D3, D4, D5: WS2812B; LED_WS2812B_PLCC4_5.0x5.0mm_P3.2mm
H1, H2: MountingHole; MountingHole_3.2mm_M3
J6: OpenMV Conn; JST_XH_B4B-XH-A_1x04_P2.50mm_Vertical
R1, R2: 10k; R_Axial_DIN0207_L6.3mm_D2.5mm_P10.16mm_Horizontal
U1, U2, U3, U4, U5: VL53L0X_horizontal
U6: MOUDLE14P-2.54-21X17.8MM

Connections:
+3V3: R1.2, R2.2, U1.1 (3V3), U2.1 (3V3), U3.1 (3V3), U4.1 (3V3), U5.1 (3V3), U6.12 (3V3)
+5V: D1.1 (VDD), D2.1 (VDD), D3.1 (VDD), D4.1 (VDD), D5.1 (VDD), U6.14 (5V); also elsewhere on the board
GND: D1.3 (VSS), D2.3 (VSS), D3.3 (VSS), D4.3 (VSS), D5.3 (VSS), U1.2 (GND), U2.2 (GND), U3.2 (GND), U4.2 (GND), U5.2 (GND), U6.13 (GND); also elsewhere on the board
unnamed: D1.2 (DOUT), D2.4 (DIN)
unnamed: D2.2 (DOUT), D3.4 (DIN)
unnamed: D3.2 (DOUT), D4.4 (DIN)
unnamed: D4.2 (DOUT), D5.4 (DIN)
RX: U6.8 (RX/D7); also elsewhere on the board
SCL: R1.1, U1.3 (SCL), U2.3 (SCL), U3.3 (SCL), U4.3 (SCL), U5.3 (SCL), U6.6 (D5/SCL)
SDA: R2.1, U1.4 (SDA), U2.4 (SDA), U3.4 (SDA), U4.4 (SDA), U5.4 (SDA), U6.5 (D4/SDA)
TX: U6.7 (D6/TX); also elsewhere on the board
WS2812B: D1.4 (DIN), U6.10 (D9)
XSHUT1: U1.5 (XSHUT), U6.1 (D0/A0)
XSHUT2: U2.5 (XSHUT), U6.2 (D1/A1)
XSHUT3: U3.5 (XSHUT), U6.3 (D2/A2)
XSHUT4: U4.5 (XSHUT), U6.4 (D3/A3)
XSHUT5: U5.5 (XSHUT), U6.9 (D8)

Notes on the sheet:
XIAO
CONN
WS2812B
VL53L0X



Board: 2 copper layers, 100.0 x 30.0 mm, 16 parts (4 on the bottom side), 17 nets.

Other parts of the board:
J1: OpenMV Conn; JST_XH_B4B-XH-A_1x04_P2.50mm_Vertical

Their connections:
+5V: J1.1; also elsewhere on the board
GND: J1.4; also elsewhere on the board
RX: J1.2; also elsewhere on the board
TX: J1.3; also elsewhere on the board

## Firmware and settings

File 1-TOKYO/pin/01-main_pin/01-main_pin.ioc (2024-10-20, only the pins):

Mcu.UserName=STM32F446RETx
PA0-WKUP.Signal=UART4_TX
PA1.Signal=UART4_RX
PA10.Signal=USART1_RX
PA11.Signal=S_TIM1_CH4
PA2.Signal=USART2_TX
PA3.Signal=USART2_RX
PA5.Signal=S_TIM2_CH1_ETR
PA6.Signal=S_TIM3_CH1
PA7.Signal=S_TIM3_CH2
PA8.Signal=S_TIM1_CH1
PA9.Signal=USART1_TX
PB0.Signal=S_TIM3_CH3
PB1.Signal=S_TIM3_CH4
PB10.Signal=I2C2_SCL
PB3.Signal=I2C2_SDA
PB8.Signal=I2C1_SCL
PB9.Signal=I2C1_SDA
PC0.Signal=ADCx_IN10
PC1.Signal=ADCx_IN11
PC10.Signal=USART3_TX
PC12.Signal=UART5_TX
PC5.Signal=USART3_RX
PC6.Signal=USART6_TX
PC7.Signal=USART6_RX
PD2.Signal=UART5_RX

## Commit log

2024-02-23 add main
    [01-main.kicad_pcb, 01-main.kicad_sch]
2024-03-20 祝日は進捗を生む日
    [01-main.kicad_sch, 02-top.kicad_pcb, 02-top.kicad_sch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]
2024-03-20 基板は5つだぜ
2024-03-22 全国行きたかった
    [01-main.kicad_sch, 03-front.kicad_pcb, 03-front.kicad_sch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]
2024-04-28 がんばる
    [01-main.kicad_pcb, 01-main.kicad_sch, 02-top.kicad_pcb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]
2024-04-28 基板は6つ
2024-05-07 ラインセンサ完成
    [04-line-CuBottom.gbr, 04-line-CuTop.gbr, 04-line-EdgeCuts.gbr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]
2024-05-07 前けずった
    [04-line.kicad_pcb, 04-line.kicad_sch]
2024-06-23 いっぱい増えた
    [01-main.kicad_sch, 02-top.kicad_sch, 03-front.kicad_sch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]
2024-11-24 KANTOプロジェクト始動
    [01-MAIN.kicad_pcb, 01-MAIN.kicad_sch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]
2024-12-10 作ってる
    [01-MAIN.kicad_sch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]
2025-01-05 かんぺきなきばん
2025-01-13 NAGOYA機設計開始
    [01-MAIN.kicad_pcb, 01-MAIN.kicad_sch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]
2025-01-13 FRONT回路設計終わった
    [03-FRONT.kicad_sch]
2025-01-13 03-FRONT部品割り当て終わり
    [03-FRONT.kicad_sch]
2025-01-13 03-FRONT部品配置終わり
    [03-FRONT.kicad_pcb, 03-FRONT.kicad_sch, 09-ToF_mod.kicad_pcb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]
2025-01-13 05-PWR回路設計完了
    [05-PWR.kicad_sch]
2025-01-13 03-FRONT 3Dモデル出力
    [05-PWR.kicad_pcb, 05-PWR.kicad_sch]
2025-01-17 01-MAIN回路図終わり
    [01-MAIN.kicad_sch, 03-FRONT.kicad_pcb, 05-PWR.kicad_pcb]
2025-01-19 03-FRONT XIAOに変更
    [03-FRONT.kicad_pcb, 03-FRONT.kicad_sch]
2025-01-19 06-UI完成
    [03-FRONT-CuBottom.gbr, 03-FRONT-CuTop.gbr, 03-FRONT-EdgeCuts.gbr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]
2025-01-23 01-MAIN部品配置完了
    [01-MAIN.kicad_pcb, 01-MAIN.kicad_sch, 05-PWR.kicad_pcb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]
2025-01-26 01-MAIN基板設計完了
    [01-MAIN.kicad_pcb, 01-MAIN.kicad_sch]
2025-01-28 04-RESCUE完了。全基板あとシルクだけ
    [04-RESCUE.kicad_pcb, 04-RESCUE.kicad_sch, 05-PWR.kicad_pcb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]
2025-02-06 つかれた
    [01-MAIN-CuBottom.gbr, 01-MAIN-CuTop.gbr, 01-MAIN-EdgeCuts.gbr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]
